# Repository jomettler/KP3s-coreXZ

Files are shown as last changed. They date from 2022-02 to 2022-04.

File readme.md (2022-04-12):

# Kingroon KP3s CoreXZ MOD / 'HALFWIRE'

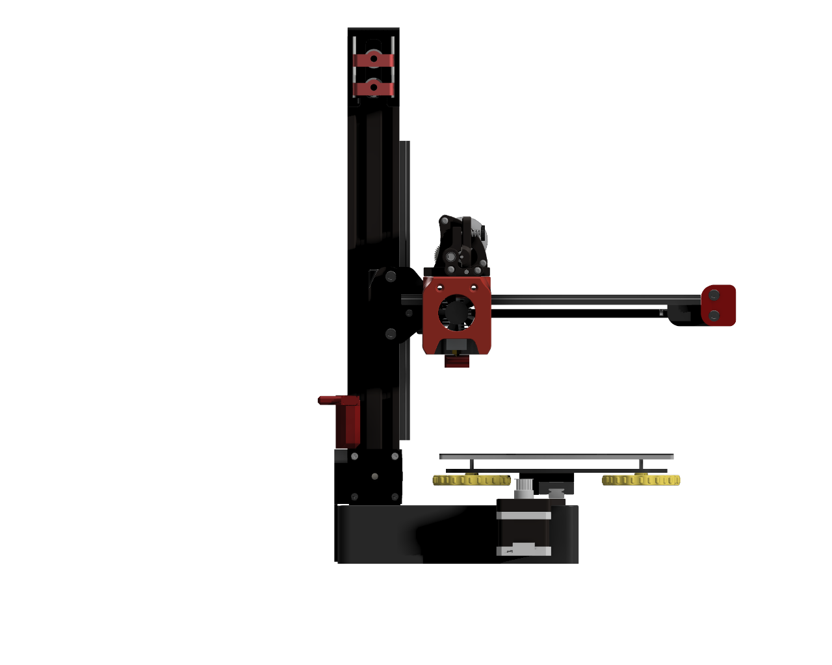
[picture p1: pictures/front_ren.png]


## BOM: 
Parts you receive from disassembling the Stock KP3s are not listed in the BOM. Please make sure you don´t loose any screws!
There is no guarantee that this BOM covers all parts necessary to build this Mod. It´s strongly recommendended to source higher quantities than listed here.

### Toolhead + Toolhead Mount
For the parts required to build the sailfin extruder, please refer to https://github.com/CroXY3D/Sailfin-Extruder
For the parts required to build the Z-Probe, please refer to https://github.com/oldfar-t/Side-Swipe-Magnetic-Probe Note, that the Probe is mounted with 3x M3x10 & 3x M3 TNut on the Z-Axis extrusion

- 2x M3x45
- 4x M3x12
- 4x M3x8 OR M3x10
- 2x 4010 radial Fan
- 1x 3010 axial Fan
- 1x V6 Hotend
- 6x HeatInsert M3x5

### XZ:
- 11x M3x8
- 31x M3x12
- 2x M3x15
- 4x M3x20
- 2x M5x12
- 4x M5x30
- 2x M5x35 
- 18x M3x5 Heat inserts
- 20x F695-2RS
- 1x 20T	Pully	
- 2x 6x1300mm Belt
- 19x M3N6 T nuts
- 6x M5 Nut	
- 1x MGN12-C 220mm Linear Rail
- 4x M3x50 fully threaded

### KeyBak:
- 4x M3x5 HeatInsert
- 1x M5 Nut
- 4x M3x12
- 1x KeyBak
- 1x M5x16
- 2x F695-2RS

### Y:
- 1x NEMA17
- 1x 20T Pully
- 17x M3x8
- 12x M3x5 HeatInsert
- 2x M3x12
- 1x M3x15
- 4x M3x16 (Option TriPoint Bed)
- 4x M3x12 (Option orig. Bed)

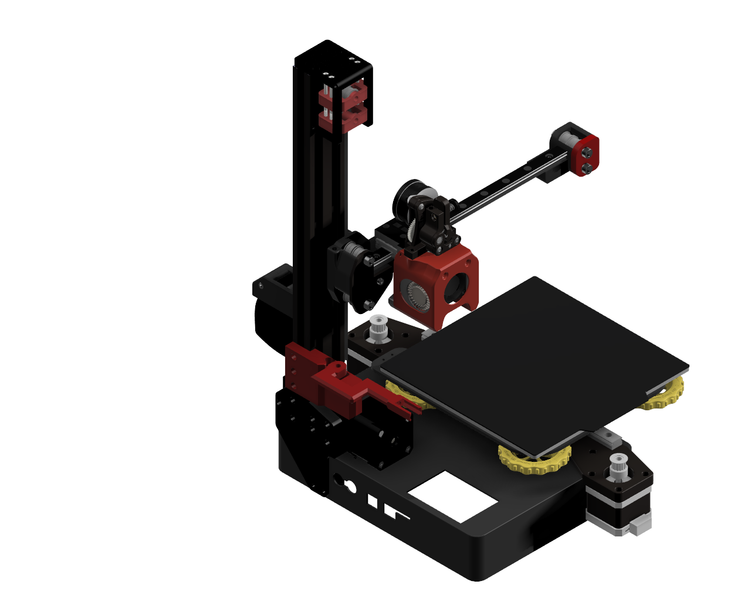
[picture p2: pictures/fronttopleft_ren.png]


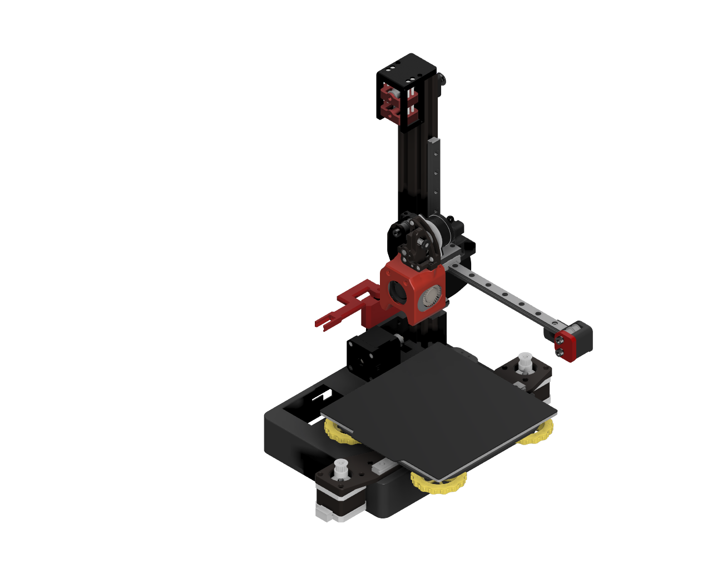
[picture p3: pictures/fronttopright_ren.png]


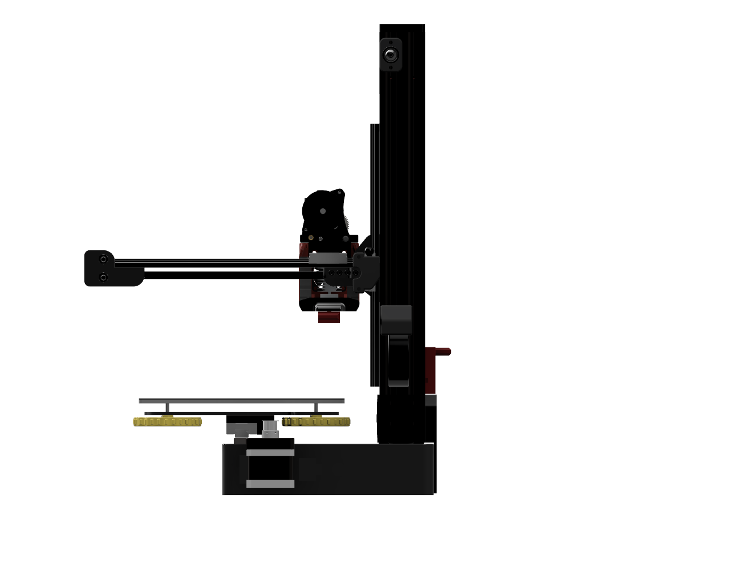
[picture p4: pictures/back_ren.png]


## Updates:
Some things will get updated (hopefully soon), some things probably won´t due to lack of time. Please note that in order to make things better, I need to be aware of issues. Feel free to open an issue, or if you fixed something, to open a PR!

## Disclaimer:
This Mod comes with absolutely no warranty and there is no guarantee that developement will be continued in the future. If you want to raise awareness to any issue connected to this Mod, please open an issue here on github. In case you have any further legal questions, please read the license file.

## Credits:
- @screech24 for testing, building the first one and raising awareness to several issues 
- @eriroh for developing the inital idea and developement support from the first scratch to the final design
- This MOD was inspired by the Armchair-Engineering P-REXZ (https://github.com/Armchair-Engineering/P-REXZ) and the VORON Switchwire (https://github.com/VoronDesign/Voron-Switchwire)
- Toolhead: Mod of https://github.com/KurioHonoo/Mini-AfterSherpa
- Extruder: https://github.com/CroXY3D/Sailfin-Extruder
- Z-probe: Mod of https://github.com/oldfar-t/Side-Swipe-Magnetic-Probe
- Keybak: Mod of https://github.com/VoronDesign/Voron-Switchwire

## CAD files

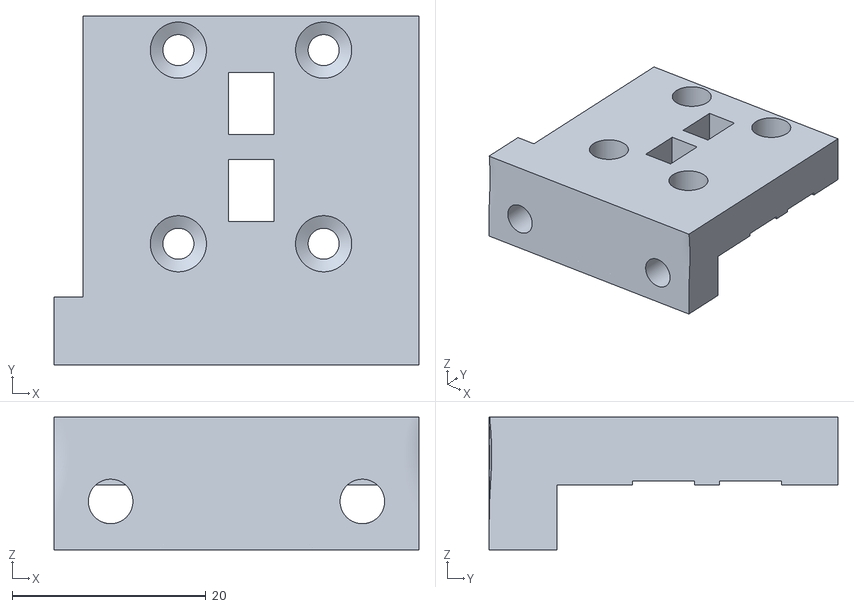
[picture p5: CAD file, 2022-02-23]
STL/BeltClipMGN9_Toolhead/Toolhead_Mount.stl
37.7 x 36.0 x 13.7

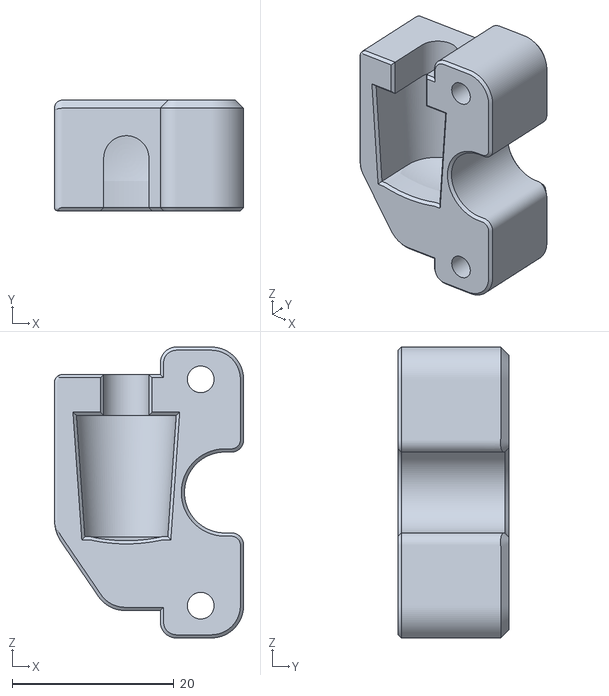
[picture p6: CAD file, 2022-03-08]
STL/Gucci/keybak_gantry_anchor.stl
23.4 x 13.7 x 36.0

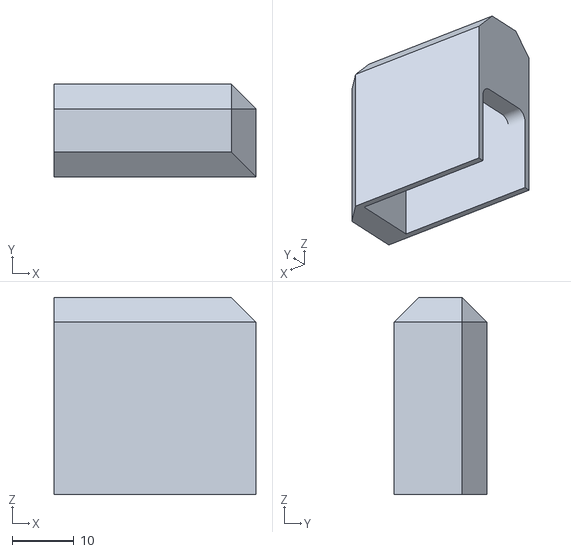
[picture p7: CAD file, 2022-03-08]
STL/Klicky/ServoHide.stl
32.8 x 15.0 x 32.0

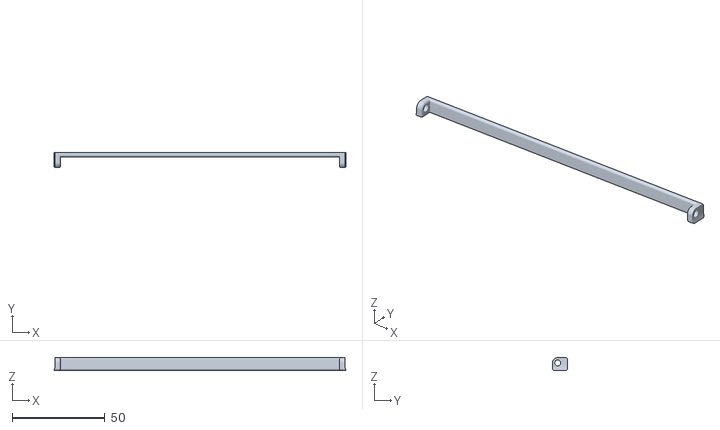
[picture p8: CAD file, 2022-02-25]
STL/X/X_Stabilizer.stl
157.5 x 8.30 x 6.90

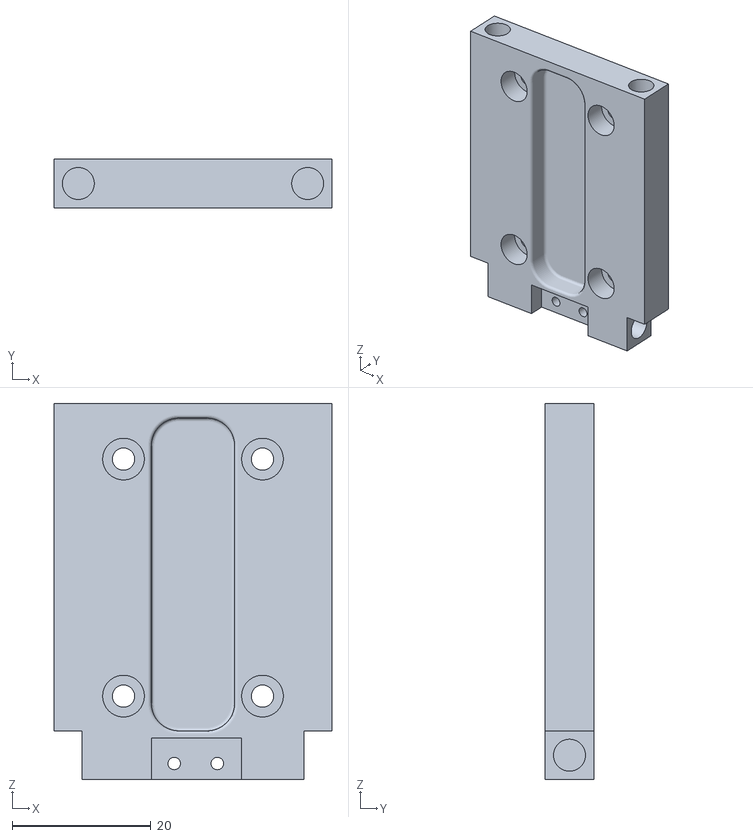
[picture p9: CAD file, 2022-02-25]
STL/XZ_Tensioner/BaseUpdated.stl
40.0 x 7.00 x 54.1

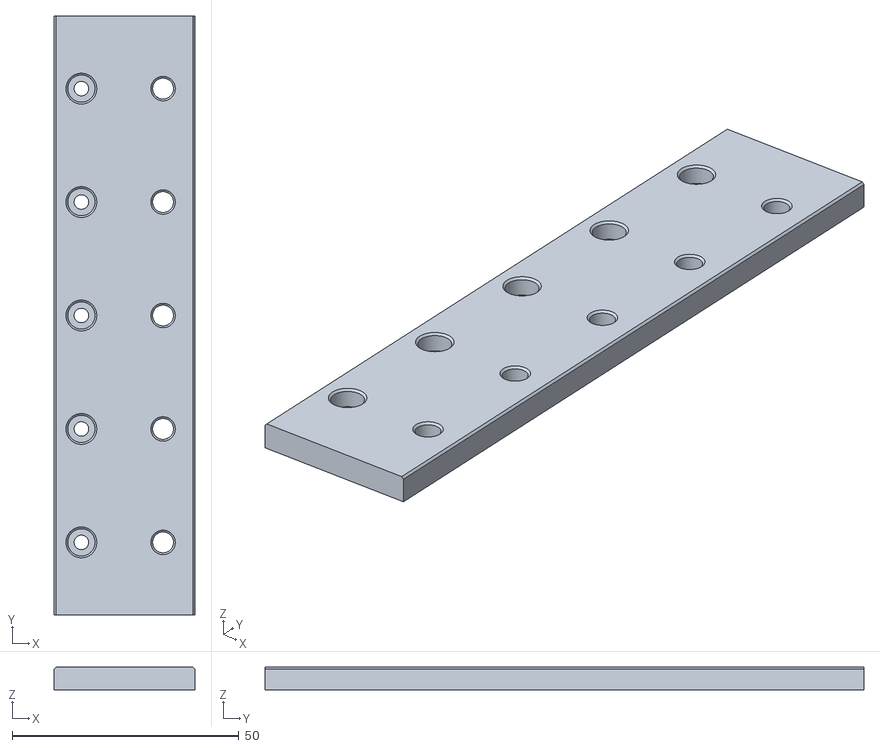
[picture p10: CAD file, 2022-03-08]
STL/Y/RailMount.stl
31.0 x 132.0 x 5.00

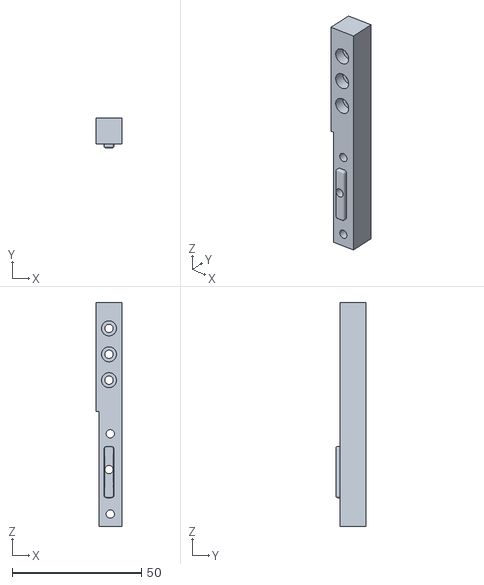
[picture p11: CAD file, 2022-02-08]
STL/ZMount/Z-Mount3.stl
10.0 x 11.5 x 86.5

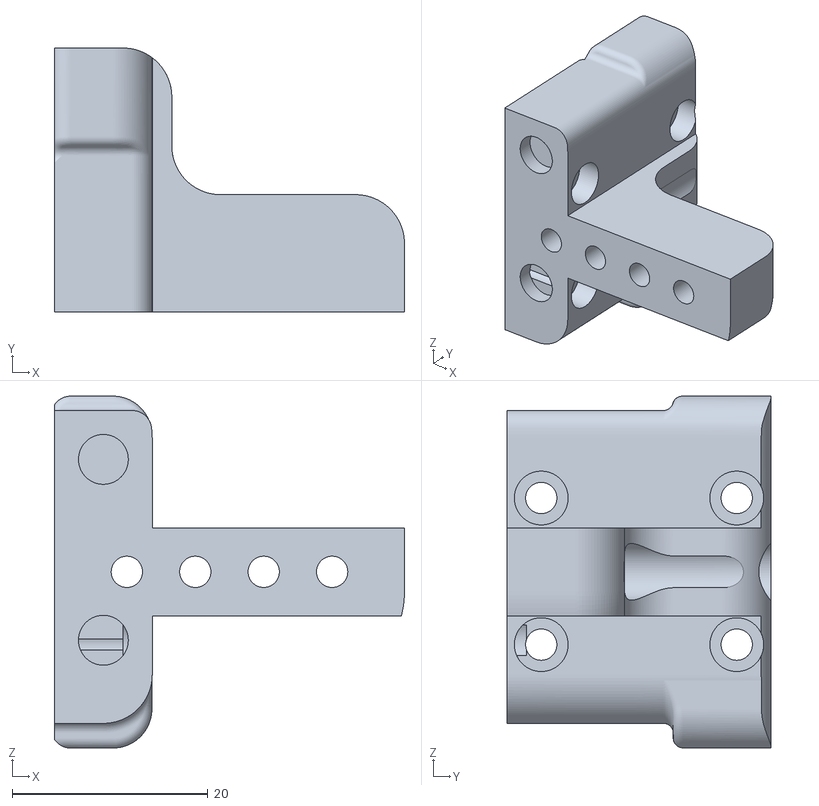
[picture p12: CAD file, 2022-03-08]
STL/ZXJoint/ZXJoint_3.stl
35.8 x 27.0 x 36.0

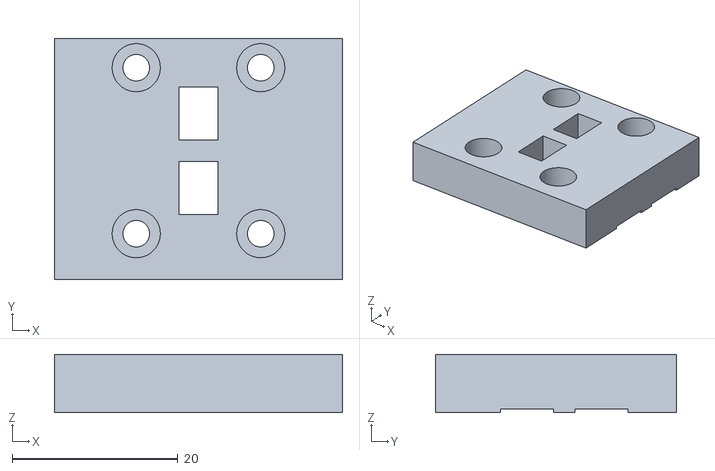
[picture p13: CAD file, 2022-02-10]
STL/BeltClipMGN9_Toolhead/Top.stl
34.7 x 29.0 x 7.00

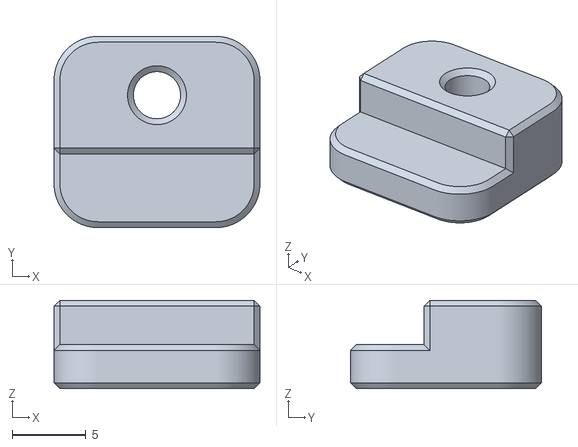
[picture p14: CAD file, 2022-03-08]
STL/Gucci/TriP_BedMountLock.stl
14.0 x 13.0 x 6.00

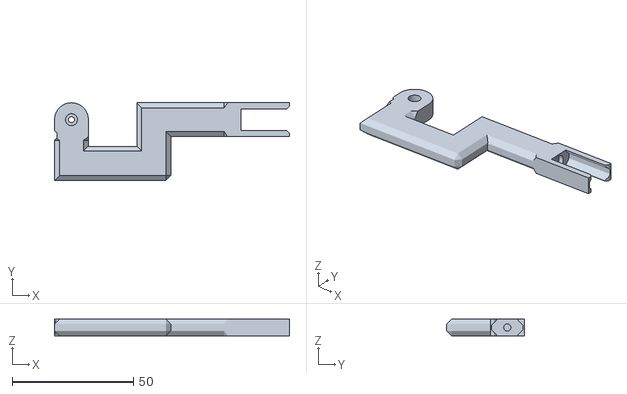
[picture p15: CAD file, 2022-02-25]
STL/Klicky/Arm.stl
97.0 x 32.0 x 7.00

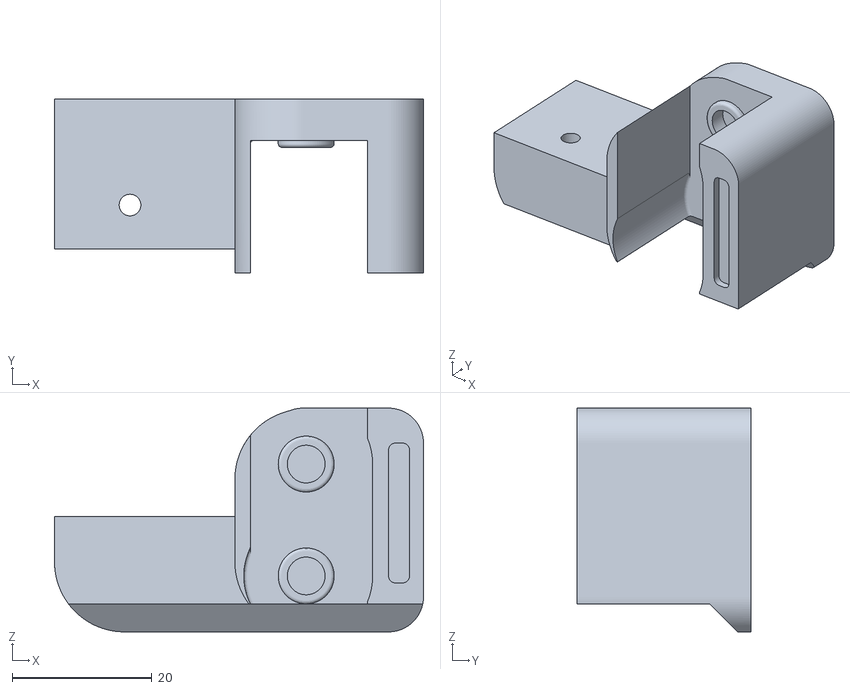
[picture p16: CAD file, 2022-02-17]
STL/X/X_2.stl
52.8 x 25.0 x 32.0

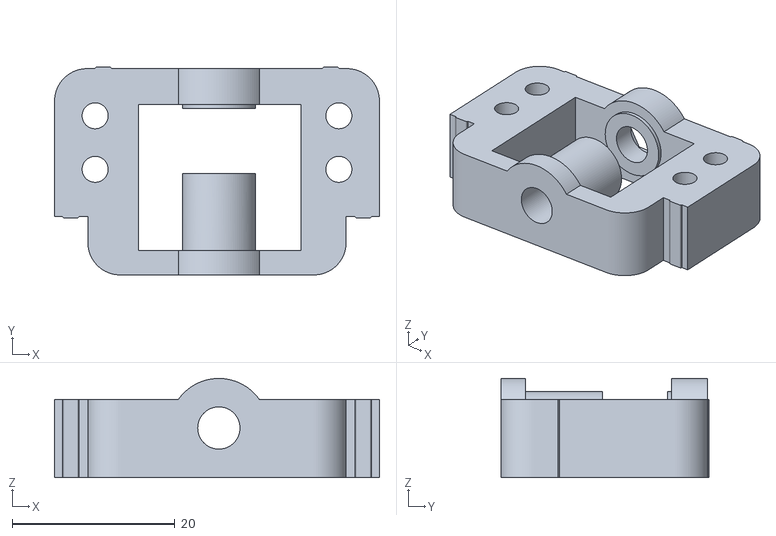
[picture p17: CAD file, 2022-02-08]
STL/XZ_Tensioner/HolderA.stl
40.0 x 25.6 x 12.2

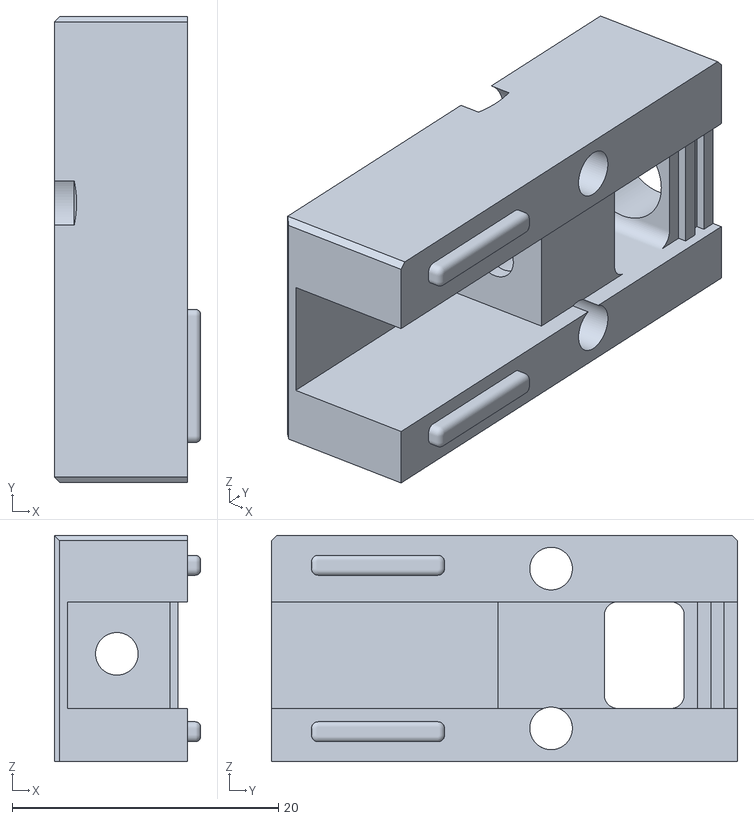
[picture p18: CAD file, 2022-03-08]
STL/Y/BedMountLock.stl
11.0 x 35.0 x 17.0

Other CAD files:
STL/ZMount/Z-Mount5.stl
STL/ZXJoint/ZXJoint_V2.stl
STL/BeltClipMGN9_Toolhead/Bottom.stl
STL/Gucci/TriP_BedMountBase.stl
CAD/Parts/XZJoint.f3d
CAD/Parts/XZ_Tensioner.f3d
CAD/Parts/X_Idler.f3d
CAD/Parts/Z-Mount.f3d
STL/Gucci/keybak_idler_bracket.stl
STL/Gucci/keybak_mount.stl
STL/Gucci/keybak_mount_plate.stl
STL/Klicky/KlickyMount_MiniAfterSherpa.stl
STL/Klicky/Probe.stl
STL/Klicky/ServoMount.stl
STL/X/X_1.stl
STL/X/X_2_shorterScrew.stl
STL/X/X_Spacer_3.stl
STL/X/X_Spacer_4.stl
STL/X/X_Stabilizer_5.stl
STL/XZ_Tensioner/Base.stl
STL/XZ_Tensioner/HolderB.stl
STL/XZ_Tensioner/LockL.stl
STL/XZ_Tensioner/LockR.stl
STL/XZ_Tensioner/Top.stl
STL/Y/BedMountBase.stl
STL/Y/BedMountTensioner.stl
STL/Y/NemaMountBack.stl
STL/Y/NemaMountFront.stl
STL/ZMount/Z-Mount1.stl
STL/ZMount/Z-Mount2.stl
STL/ZMount/Z-Mount4.stl
STL/ZXJoint/ZXJoint_1.stl
STL/ZXJoint/ZXJoint_2.stl
STL/ZXJoint/ZXJoint_4.stl
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

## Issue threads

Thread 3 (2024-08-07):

Belt path

Ciax869, 2024-08-07:
@jomettler Do you have any image of the belt path?
This does not seem to work.

jomettler, 2024-08-08:
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

I changed the XY Joint and Toolhead, but never updated it here. You are correct, that the uploaded version has indeed wrong mounting, one belt needs to attach below and the other one above the X Axis, like you can see in the picture.
I also changed to a bowden toolhead and moved the probe dock into the XZ Joint and used Euclid Probe instead of the klicky-like probe. I´ld also recommend to support the X Axis e.g. with a meakerbeam or makerbeam XL (the XL would require some changes to the XZ Joint and X Axis Idler to make room for it) as I broke the X Idlers multiple times.

jomettler, 2024-08-08:
Here you can see the updated toolhead and the old XZ Joint with sensorless homing
https://github.com/user-attachments/assets/a1af553e-db24-49d6-87b8-f7a274874d73

Ciax869, 2024-08-08:
Cool thanks. I am currently building it. Mind uploading your current state to git? I would like to steal the euclid probe mount 😄 Maybe the x axis could be supported with the bottom case connector thingy (seen in the uploaded photo). My CAD skills are bad. Maybe i am going to try it. Thank you for your help!
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

jomettler, 2024-08-08:
@Ciax869
[KP3s.zip](https://github.com/user-attachments/files/16540586/KP3s.zip)

ZIP File contains the Y Axis and XZ Joint+Toolhead
It might be sufficient to beef up the X Idler housing a little bit and "support" the X Rail with a big printed blog. The printed part would probably do nothing for the X Rail, but would help with the twisting of the Idler housing, which could be enough.
Sidenote: For a bowden toolhead, the keyback is no longer necessary, I didnt notice any gantry sagging.

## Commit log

2022-01-17 Add CAD files
2022-01-27 Update + BOM fix
    [BOM.ods]
2022-01-28 Update BOM
    [BOM.ods]
2022-02-08 update STL
    [Base.stl, HolderA.stl, HolderB.stl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]
2022-02-09 add f3d parts
    [XZIdler v1.f3d, XZJoint.f3d, XZ_Tensioner.f3d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]
2022-02-10 add BeltClip MGN on X to enable test belt-path
    [Bottom.stl, Top.stl]
2022-02-17 add short screw version X
    [X_1_shorterScrew.stl, X_2_shorterScrew.stl]
2022-02-23 Upload AfterSherpaMount
    [Top_AfterSherpaMount.stl]
2022-02-23 Add Klicky
    [Arm.stl, KlickyMount_MiniAfterSherpa.stl, Probe.stl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]
2022-02-24 Update ServoMount/Fix cable troubles
    [ServoMount.stl]
2022-02-24 add toolhead, update klicky mount
    [KlickyMount_MiniAfterSherpa.stl]
2022-02-25 Update Stabilizer and XZJoint
    Update increases X-Length by 25mm and includes a Screwmount on XZ Joint as endstop Point for ZMax Endstop
    [X_Stabilizer_Update.stl, ZXJoint_V2.stl]
2022-02-25 Update Base Tensioner for Z Max Endstop
    [BaseUpdated.stl]
2022-02-26 Update Y, Add Gucci, Add CAD, Update Pics
    [BedMountBase.stl, BedMountLock.stl, BedMountTensioner.stl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]
2022-03-08 update for public repo
    [BedMountBase.stl, BedMountLock.stl, NemaMountBack.stl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]
